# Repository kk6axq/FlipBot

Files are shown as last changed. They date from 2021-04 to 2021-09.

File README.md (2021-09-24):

# FlipBot
FlipBot is a small two wheeled robot development platform. It was developed over the Spring 2021 semester as an honors contract project for EGR102, at Arizona State University on the Polytechnic Campus, under the guidance of Dr. Daniel Frank. The goal for this project was to develop a small robot platform and to gain a better understanding of the design considerations in designing a complete system. Where possible, this project attempted to integrate components directly into the design, rather than using breakout boards or modules.
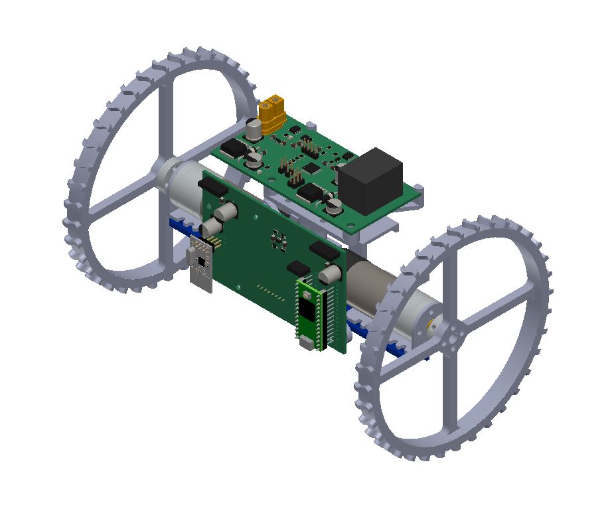
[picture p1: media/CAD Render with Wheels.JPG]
Project Photo


 ## Components
 There are several major components of FlipBot:
 * **Controller.** The robot is controlled by a wireless remote connected to a Wii Nunchuk. This provides a joystick, two buttons, and pitch/roll data that is processed by a microcontroller and sent wirelessly to the main controller onboard the robot. The controller also has onboard battery management hardware to enable operation from a single 18650 battery.
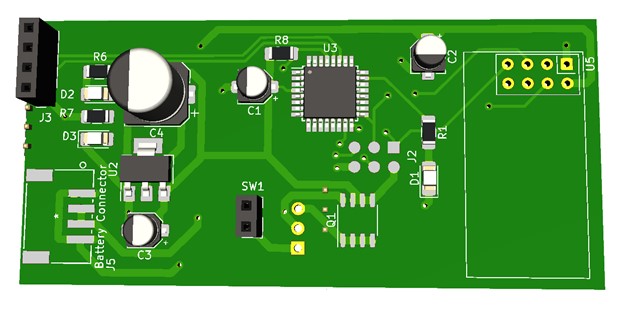
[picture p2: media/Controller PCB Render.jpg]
Controller PCB
 

 * **Wireless link.** The controller and robot use NRF24 radio modules to communicate. These operate in the 2.4GHz ISM band and provide low latency, medium range. While they have the ability to confirm packet reception, in this application the controller sends packets regardless of whether the received is in range or able to respond.
 * **Onboard Power Management.** This project was developed in conjunction with a second honors contract to develop a power management board for use with LiPo batteries. This PCB provides intelligent power monitoring capabilities on the robot. More information about this part is available in the project repository: [https://github.com/kk6axq/PowerMonitor/](https://github.com/kk6axq/PowerMonitor/).

PCB Photo

 * **Orientation Sensing.** An onboard MPU6050 accelerometer/gyro provides onboard orientation detection, enabling the controls to be reversed if the robot flips upside down.
 * **Main Board.** The main PCB interfaces to the radio, orientation sensor, and the power management board, in addition to providing motor control and processing input from the motor's encoders (not yet implemented).
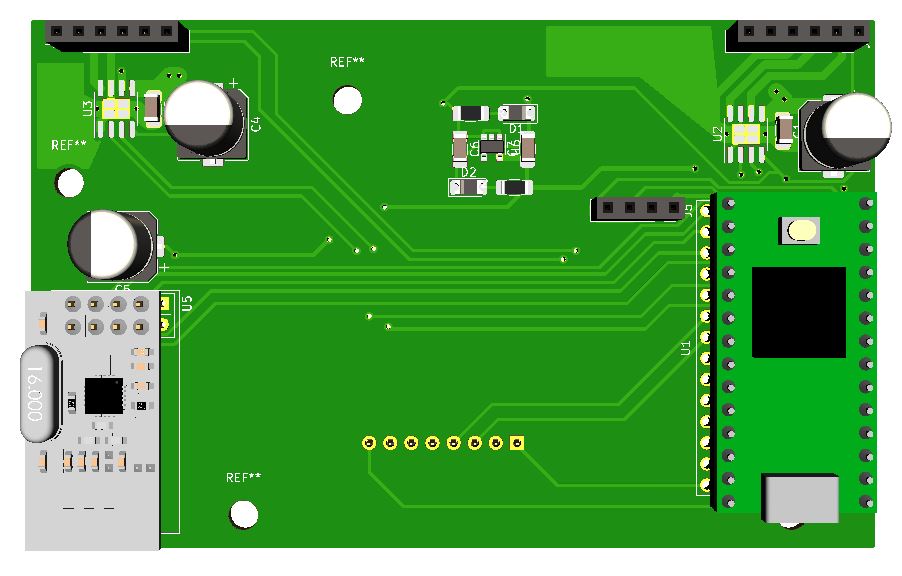
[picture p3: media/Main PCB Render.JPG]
Main PCB


## Project Status
Due to incomplete design verification and limited time, the project was not able to achieve full functionality before the end of the semester. The level converter responsible for interfacing between the motor controllers and the microcontroller was not properly matched to the application and would not properly convert, leading the motor controllers to operate sporadically.

This issue, in addition to a few minor routing decisions, is due to be fixed during a revision of the main board scheduled for Summer 2021, with the hope that the project will be functional by Fall 2021.

**Update Fall 2021:** Over the summer, the hardware design issues were mitigated within the existing PCB and a new PCB was milled for the controller. There still remain some phantom issues with controller connectivity and some larger issues with the initial current draw of the motor controllers. At this point, the project is at a holding point, and may or may not see further development.

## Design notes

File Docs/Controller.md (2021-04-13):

# Controller
The controller provides wireless teleoperation capabilities to the robot. It is powered by an ATTiny88 microcontroller with a Wii Nunchuk joystick for human input and an NRF24 radio for wireless communication.

Controller PCB Render

Controller PCB Render from KiCAD

## Input
A Wii Nunchuk controller is used for input. The controller receives 3.3V and communicates over I2C with the microcontroller. It provides a joystick, two buttons, and pitch and roll estimation, enabling multiple different control schemes. Rather than convert these into motor commands onboard, the controller sends this raw data to the robot where the selected inputs are used to calculate motor values.

## Protocol
For ease of communication, the microcontroller sends a packet consisting of a `struct` that holds all the input fields and has been converted to a byte array. The packet is sent with no acknowledgement, meaning that it will continue to send even if the robot is not in range. This could be beneficial in situations with spotty range, but comes at the cost of increased power consumption.

The `struct` and its byte array conversion are defined as follows:
```
struct RobotMsg {
  byte linear;
  byte angular;
  bool buttonC;
  bool buttonZ;
  float rollAngle;
  float pitchAngle;
};

typedef union {
  RobotMsg msg;
  byte buffer[sizeof(RobotMsg)];
} convert;
```

## Power
The controller is powered by a single 18650 Lithium Ion battery. An onboard battery manager provides a micro USB charging port and an onboard boost converter outputs a steady 5V for the main systems. The runtime on a full charge has not yet been calculated, and likely will not be, as the project used salvaged batteries that likely have lower than spec capacities.

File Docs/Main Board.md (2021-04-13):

# Main Board
The main PCB interfaces with all the major components of the robot. The core of the board is a Teensy 3.2 microcontroller, which was selected for the large number of interrupts and processing power available to handle high speed encoder measurement. The functions of the board can be roughly divided into three sections: communications, sensing, and output.

Main PCB Render

Main PCB Render from KiCAD.

## Communications
The board communicates with the controller using an NRF24 radio module. The received command packets, detailed more thoroughly in the controller documentation, are processed, fused with sensor data, and converted into motor commands.

Programming and serial monitoring is handled over the Teensy's onboard USB connector. Due to backfeeding concerns, the VUSB jumper on the Teensy was cut, meaning that it can only be programmed when the board is receiving through the external 5V supply pins.

## Sensing
The two major sensors on board are the MPU6050 accelerometer/gyro, and the power management board. The MPU6050 is currently used to measure the direction of the gravity vector for determining orientation. Depending on the orientation, the controls may be swapped to ensure the driver can continue to operate it normally.

The power management board provides connections for a monitoring port, where the Teensy could receive data on current draw, voltage, and fault states. Currently, there is no need for this in the system, and thus it is not implemented. The Teensy does not do anything that requires a shutdown procedure, so there was not a need for it to monitor the power, as it will automatically be turned off if fault conditions exist. This link could be used for possible additional features, including:
* **Safe shutdown of the payload.** If there were a payload like a Raspberry Pi, it would be useful to know when power is going to be cut so the computer could be safely shutdown.
* **Voltage indicator on controller.** Currently, the controller only communicates to the main board, but a future design could include an indicator LED for battery status and a signal could be sent to the controller to indicate that.
* **Automatic docking/recharging.** If the project were to become autonomous, monitoring the power could enable it to return to a docking station for more power.
* **Current restriction.** The main board could throttle the motors based on the current draw to optimize battery life or detect stall conditions.

## Output
The output system consists of a level converter and two motor controllers. The current revision uses the TXB0108 bidirectional level converter and two A4950 3.5A motor driver ICs. The level converter does not currently interface well with the motor controllers, likely because of the direction sensing not handling the current draw of the motor controllers well, and it will be replaced in the next revision. The motor controllers have been a bit temperamental, but appear to work well when they are installed undamaged. Together, they drive two Pololu 34:1 geared DC motors that can each provide around 63 oz-in of torque at 2.1A current draw.

Once the level shifter is replaced, the interface should be fairly straightforward, as other motor controllers using the same chipset just send normal PWM signals.

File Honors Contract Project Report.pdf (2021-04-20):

## FlipBot: Small Robot Development Platform Design Report for EGR102 Honors Enrichment Contract April 13, 2021 Lukas Severinghaus Introduction:

This project was completed for an Honors Enrichment Contract in EGR102, Foundations of Engineering Design Project II, at Arizona State University. The goal of this project was to develop a small two wheeled robot for use as a low-cost development platform in inspection applications. Rather than assembling a collection of modules, this project focused on whole system integrated development, furthering my personal interest in exploring the steps behind developing a robot system from the ground up. This honors enrichment contract was run in conjunction with a second honors enrichment contract in EGR216, under the guidance of Dr. Ayan Mallik, to develop the power management component of the robot. Ultimately, this project is still ongoing, and has been, and will be, a valuable learning experience for my personal development as an engineer. This report examines the project through the steps of the engineering design process: Empathize, Define, Ideate, Prototype, and Test.

## Empathize:

The idea from this project came from when I toured a US Army Robotics R&D lab several years ago. I saw a robot that was designed to be tossed through a window and teleoperated so that soldiers could clear a building without ever having to step foot inside. A bit more research yielded the company behind this robot, Recon Robotics, and the robot itself, the Throwbot® 2, see Figure 1 below.

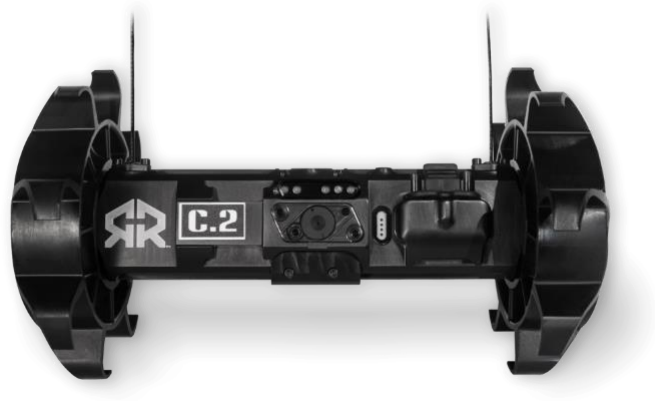
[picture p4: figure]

Figure 1. Recon Robotics Throwbot® 2 [1].

This robot retails for over $15,000, according to the GSA [2]. I was interested in learning about the development process behind a robot of this size, so I set out a few goals, and decided to build my own. In the end, I established three project criteria:

- Small size. This would allow me to use smaller components and try out surface mount components for the circuit boards.
- Drive regardless of orientation. If the robot flipped upside down, I wanted it to be able to reverse the controls so that the operator could continue to drive.
- Wireless remote control. I wanted the robot to be fully self-contained so it could run with only itself and the controller.

## Define:

Once I obtained approval for the project, the first step was to develop a block diagram. This helped define each part of the project and divided it up into small, manageable chunks. Figure 2, below, shows the block diagram for the electrical systems, where I focused most of my efforts.

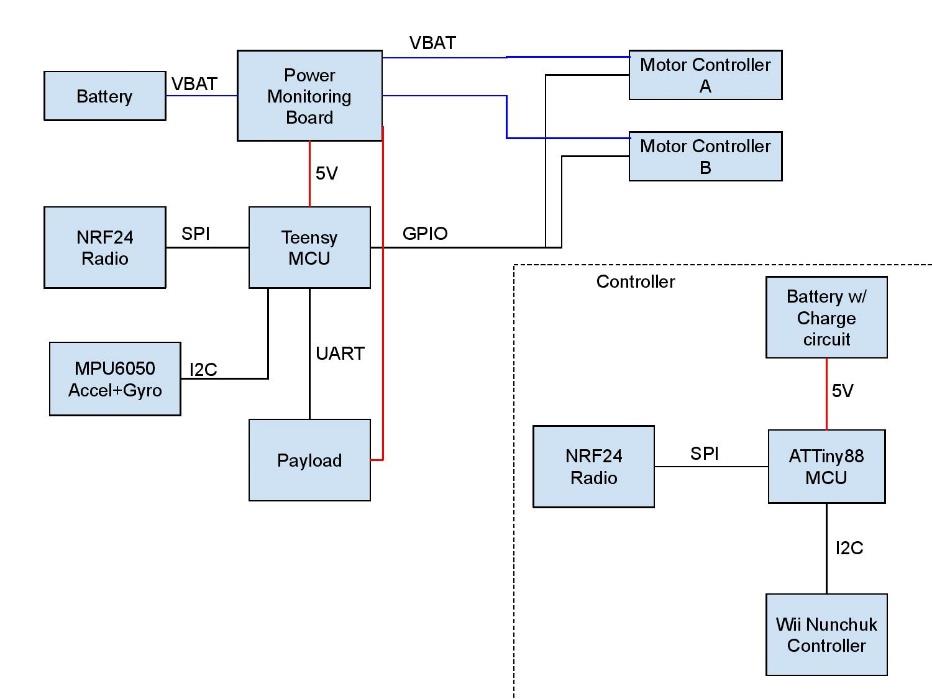
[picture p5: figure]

Figure 2. Electrical block diagram.

## Ideate:

As I finished the block diagram, I began researching each part and examining how I could implement it. I settled on a mixture of proven parts, that I had used before, and new methods, that I had not yet used. For example, I selected a Wii Nunchuk for the controller joystick, as I already had one on hand and it was more ergonomic than what I could design within the project timeframe.

For the mechanical design of the robot, I started mocking up what I wanted it to look like. The mechanical design had a large influence on the electrical design, as the printed circuit boards (PCBs) had to fit within the mechanical confines of robot. My initial CAD models were fairly crude, as I had little idea of how everything would go together, see Figure 3.

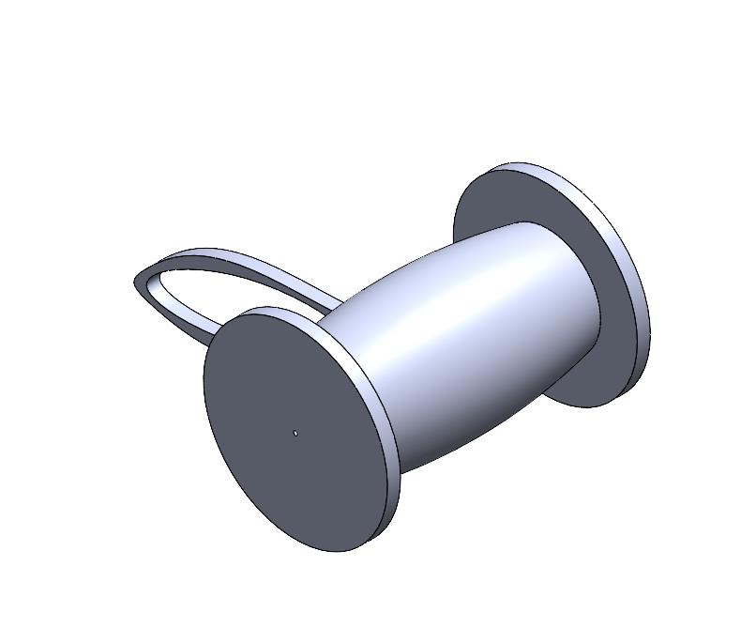
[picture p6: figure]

Figure 3. Initial CAD design with reversible tail for upside-down operation.

## Prototype:

Once I decided what parts I was going to use, I ordered a first batch of parts and assembled a breadboard prototype of the electrical system. The combined system was fairly complex and ended up covering five breadboards, but the testing helped eliminate most of the bugs in the initial designs. I used KiCAD, an open source EDA (Electronic Design Automation) program, to develop all the schematics and PCBs. These design files were then sent to the on campus PCB mill and assembled. The assembly process highlighted minor errors that had slipped past my initial breadboard testing, but ultimately no boards had to be re-milled. Figure 4 shows a render of the PCB for the wireless controller.

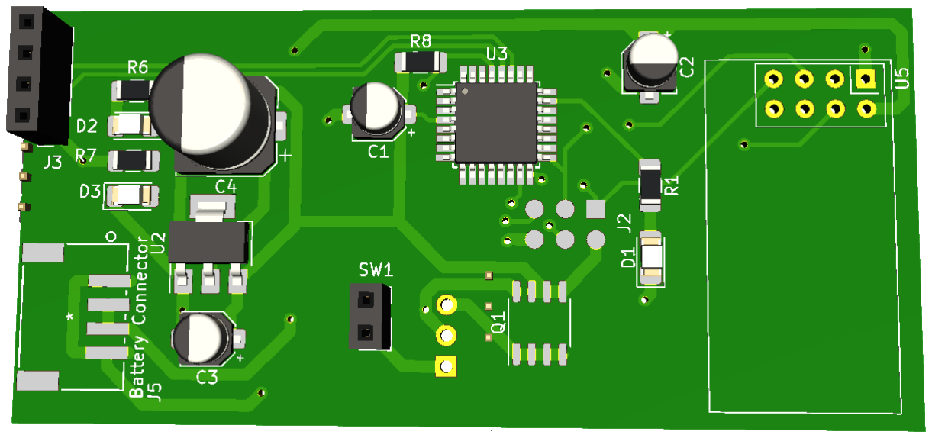
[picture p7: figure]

Figure 4. Controller PCB Render from KiCAD.

Additionally, as the PCBs reached their final forms, I used KiCAD to export STEP models of the boards into SolidWorks so I could model the mechanical design. Within the timeframe of the project, I was only able to build an initial prototype layout. While not as refined as I would have wanted, it allows easy access to all the components during testing, as shown in Figure 5.

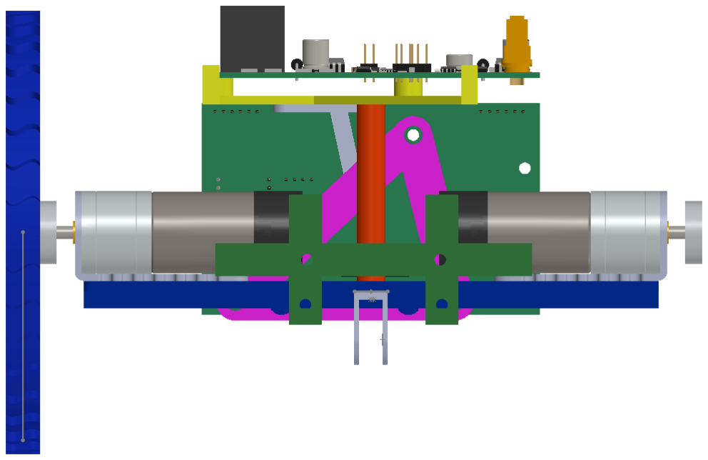
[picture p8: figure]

Figure 5. Prototype CAD assembly.

## Test:

The testing phase occupied at least half of the entire project timeline. The complexity of this project, combined with the new components I was using, made debugging a tedious, time consuming process. Ultimately, most of the bugs were ironed out, but one critical system failed to perform.

The controller’s design worked flawlessly, along with the wireless communications to the robot, and the orientation sensor, but the motor controllers, that provide power to the motors, had a fundamental design flaw. I had failed to properly breadboard test the level shifting hardware that enabled the microcontroller to communicate with the motor controllers and the parts were incompatible. By the time I came to this realization, it was too late in the semester to redesign the board, meaning the project would not be functional by the end of the semester.

## Conclusion:

Ultimately, the project was an invaluable education experience. I had the opportunity to dive into several areas I had not explored before, including:

- Multi-part 3D design and FDM printing
- Surface mount PCB design and design for integration
- Low level electrical design
- Software protocol design
- Integrated mechanical and electrical design

These are all skills that I plan to continue growing, and anticipate using, both in my education and in the workplace. Through this project, I gained an appreciation for the enormous amount of work that goes into developing a project like this. While the Honors Enrichment Contract is done, I plan to design a second revision of the electrical system to fix the issues present in the current version, with the hope that the project will be concluded in a functional state.

For more information on the project, visit: https://github.com/kk6axq/flipbot

## Acknowledgements:

The following sources were invaluable in the development of the project:

Dr. Ayan Mallik, for his assistance with the design of the power management board and for opening his lab for me to test the board.

dparson55, “dparson55/NRFLite,” GitHub. [Online]. Available: https://github.com/dparson55/NRFLite. [Accessed: 13-Apr-2021].
ElectronicCats, “ElectronicCats/mpu6050,” GitHub. [Online]. Available: https://github.com/electroniccats/mpu6050. [Accessed: 13-Apr-2021].
“Pololu - 34:1 Metal Gearmotor 25Dx67L mm MP 12V with 48 CPR Encoder,” Pololu Robotics & Electronics. [Online]. Available: https://www.pololu.com/product/4864. [Accessed: 13-Apr-2021].

## References:

[1] “THROWBOT® 2 ROBOT,” Recon Robotics. [Online]. Available: https://reconrobotics.com/products/throwbot-2-robot/. [Accessed: 13-Apr-2021].
[2] “Search Results,” U.S. General Services Administration. [Online]. Available: https://www.gsaadvantage.gov/advantage/ws/search/advantage_search?q=0:2RECONROBOTICS&db=0&searchType=0. (https://www.gsaadvantage.gov/advantage/ws/search/advantage_search?q=0:2RECONROBOTICS&db=0&searchType=0) [Accessed 13-Apr-2021].

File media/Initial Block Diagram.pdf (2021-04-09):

Battery

Power
Monitoring
Board

Motor Controller
A

Motor Controller
B

Teensy
MCU

Payload

NRF24
Radio

MPU6050
Accel+Gyro

NRF24
Radio

ATTiny88
MCU

Wii Nunchuk
Controller

Battery w/
Charge
circuit

I2C

SPI

UART

GPIO

VBAT

VBAT

SPI

I2C

5V

5V

Controller

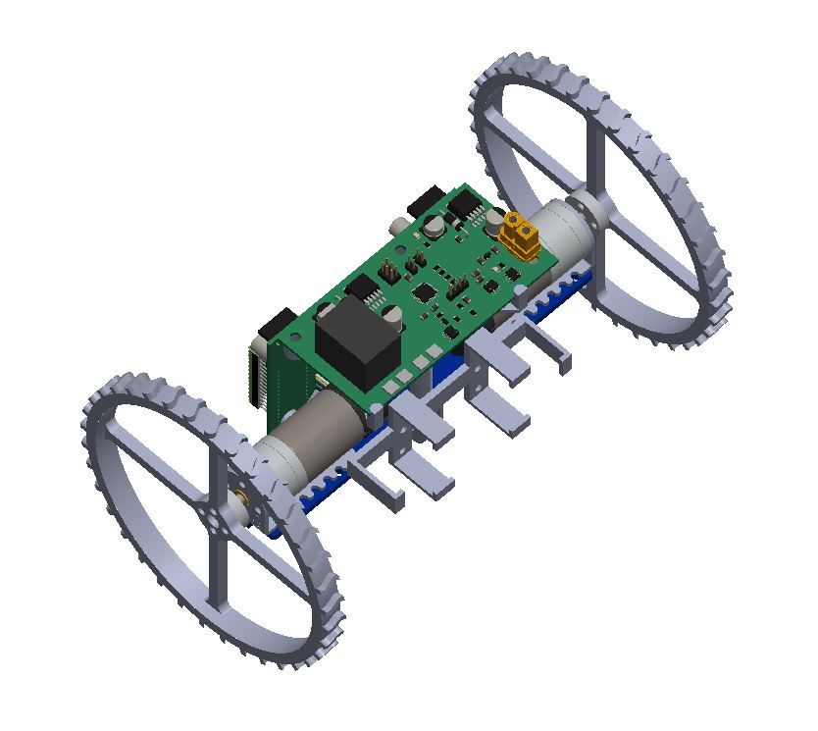
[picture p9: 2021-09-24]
media/CAD Render Rear.JPG

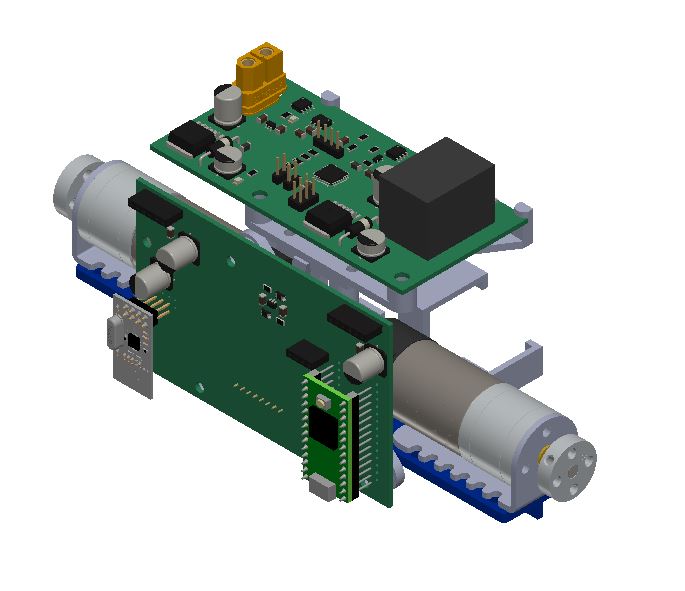
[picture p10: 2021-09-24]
media/CAD Render.JPG

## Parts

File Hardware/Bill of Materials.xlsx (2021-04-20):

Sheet: Mechanical Design
Item | Qty | Total price | Link
Gearmotor | 2 | $69.90 | https://www.pololu.com/product/4864
Hub adapter | 1 set | $6.95 | https://www.pololu.com/product/1997
Motor bracket | 2 | $14.90 | https://www.pololu.com/product/2676
Heat-set insert | ~6 | $7.49 | https://www.amazon.com/gp/product/B00Y20YLKY/
Assorted M3 hardware | Assorted | $10.99 | https://www.amazon.com/gp/product/B07CYNKLT2/

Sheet: Main Board THT
Universal Reference | Board Reference | Qty | Actual Qty | Value | Footprint | Part number | Price | Note |  | One board price |  | Line price | Status: | Ready to order
Main THT C1 C3 | C1 C3 | 2 | 10 | 0.22uF 50V X5R | THT | 445-FK28X7R1C224KN000-ND | $0.32 |  |  | $0.64 |  | $3.20
Main THT C2 C4 | C2 C4 | 2 | 10 | 100uF 50V Electrolytic | THT | 493-5916-1-ND | $0.20 |  |  | $0.41 |  | $2.05
Main THT D1 | D1 | 1 | 10 | RED |  |  |  | Already have |  | $0.00 |  | $0.00
Main THT D2 | D2 | 1 | 10 | GREEN |  |  |  | Already have |  | $0.00 |  | $0.00
Main THT J1 | J1 | 1 | 1 | Motor 1 Connector | 1x6 2.54 |  |  | Already have |  | $0.00 |  | $0.00
Main THT J2 | J2 | 1 | 1 | MPU6050 GY-521 Breakout | 1x8 2.54 |  |  | Already have |  | $0.00 |  | $0.00
Main THT J3 | J3 | 1 | 1 | Motor 2 Connector | 1x6 2.54 |  |  | Already have |  | $0.00 |  | $0.00
Main THT J4 | J4 | 1 | 1 | 5V Power | 1x2 2.54 |  |  | Amazon |  | $0.00 |  | $0.00
Main THT J5 | J5 | 1 | 1 | Payload Connector | 1x4 2.54 |  |  | Already have |  | $0.00 |  | $0.00
Main THT J6 | J6 | 1 | 1 | 12V Power | 1x2 2.54 |  |  | Amazon |  | $0.00 |  | $0.00
Main THT R1 | R1 | 1 | 10 |  |  |  |  | Already have |  | $0.00 |  | $0.00
Main THT R2 | R2 | 1 | 10 |  |  |  |  | Already have |  | $0.00 |  | $0.00
Main THT R3 R4 | R3 R4 | 2 |  | 0.1 1% 1W 2512 | THT | PPC1D.10CT-ND | $0.77 |  |  | $1.54 |  | $0.00
Main THT U1 | U1 | 1 | 1 | Teensy3.2 |  |  |  | Already have |  | $0.00 |  | $0.00
Main THT U2 U3 | U2 U3 | 2 | 2 | A4950E | SOIC-8 | 620-1400-1-ND | $2.84 | Use SMD |  | $5.68 |  | $5.68
Main THT U4 | U4 | 1 | 1 | TXB0108PWR | TSSOP20 | 296-52839-1-ND | $1.29 | Use SMD |  | $1.29 |  | $1.29
Main THT U5 | U5 | 1 | 1 | NRF24L01_Breakout | 2x4 2.54 |  |  | Amazon |  | $0.00 |  | $0.00
 |  |  |  |  |  |  |  |  | Total | $9.56 | Total price: | $12.22

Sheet: Controller THT Parts
Universal Reference | Board Reference | Qty | Actual Qty | Value | Footprint | Part number | Price | Note | One board price | Actual price | Status: | Ready to order
Controller THT C3 C1 | C3 C1 | 2 | 10 | 10uF | THT | 732-8856-1-ND | $0.10 |  | $0.20 | $1.00
Controller THT C4 | C4 | 1 | 10 | 100uF | THT | 732-8630-1-ND | $0.12 |  | $0.12 | $1.20
Controller THT C6 C5 | C6 C5 | 2 | 10 | 0.1uF | THT | 732-8962-1-ND | $0.10 |  | $0.20 | $1.00
Controller THT D1 | D1 | 1 |  | Zener 3.3V | THT | BZX85C3V3-TAPGICT-ND | $0.39 |  | $0.39 | $0.00
Controller THT D2 | D2 | 1 |  | RED |  |  |  | Already have | $0.00 | $0.00
Controller THT D3 | D3 | 1 |  | GREEN |  |  |  | Already have | $0.00 | $0.00
Controller THT J1 | J1 | 1 |  | Boost Board |  |  |  | Already have | $0.00 | $0.00
Controller THT J2 | J2 | 1 |  | AVR-ISP-6 | 2x3 2.54 |  |  | Already have | $0.00 | $0.00
Controller THT J3 | J3 | 1 |  | Nunchuk Connector |  |  |  | Already have | $0.00 | $0.00
Controller THT J4 | J4 | 1 |  | Charge Controller |  |  |  | Already have | $0.00 | $0.00
Controller THT J5 | J5 | 1 |  | Battery Connector |  |  |  | Already have | $0.00 | $0.00
Controller THT R6 | R6 | 1 |  | 330 |  |  |  | Already have | $0.00 | $0.00
Controller THT R7 | R7 | 1 |  | 220 |  |  |  | Already have | $0.00 | $0.00
Controller THT R8 | R8 | 1 |  | 10k |  |  |  | Already have | $0.00 | $0.00
Controller THT SW1 | SW1 | 1 |  | SW_SPST |  |  |  | Already have | $0.00 | $0.00
Controller THT U2 | U2 | 1 | 5 | LM1117-3.3 | THT | LM1117T-3.3/NOPB-ND | $1.64 |  | $1.64 | $8.20
Controller THT U3 | U3 | 1 | 5 | ATtiny88-AU | THT | ATTINY88-PU-ND | $1.80 |  | $1.80 | $9.00
Controller THT U4 | U4 | 1 | 2 | TXB0108DQSR | TSSOP20 | 296-52839-1-ND | $1.29 | Use SMD version | $1.29 | $2.58
Controller THT U5 | U5 | 1 |  | NRF24L01_Breakout |  |  |  | Amazon | $0.00 | $0.00
 |  |  |  |  |  |  |  |  | $5.64 | $22.98

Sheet: Controller SMD Parts
Universal Reference | Board Reference | Qty | Actual Qty | Value | Footprint | Part number | Price | Note |  | One board price | Actual price | Status: | Ready to order
Controller C3 C1 | C3 C1 | 2 | 10 | 10uF | Radial | 732-8411-2-ND | $0.17 |  |  | $0.34 | $1.70
Controller C4 | C4 | 1 | 10 | 100uF | Radial | 2616-VUJ101M1HTR-1313STR-ND | $0.12 |  |  | $0.12 | $1.20
Controller C6 C5 | C6 C5 | 2 | 10 | 0.1uF | 1206 | 732-8097-2-ND | $0.11 |  |  | $0.22 | $1.10
Controller D1 | D1 | 1 | 10 | Zener 3.3V | SMA | BZG05C3V3-M3-08GICT-ND | $0.41 |  |  | $0.41 | $4.10
Controller D2 | D2 | 1 | 10 | RED | 1206 | 160-1168-1-ND | $0.18 | Vf 2v |  | $0.18 | $1.76
Controller D3 | D3 | 1 | 10 | GREEN | 1206 | 160-1169-2-ND | $0.17 | Vf 2.1v |  | $0.17 | $1.69
Controller J1 | J1 | 1 |  | Boost Board |  |  |  | Already have |  | $0.00 | $0.00
Controller J2 | J2 | 1 | 10 | AVR-ISP-6 | 2x3 2.54 | 2057-PH2-06-UA-ND | $0.12 |  |  | $0.12 | $1.20
Controller J3 | J3 | 1 |  | Nunchuk Connector |  |  |  | Already have |  | $0.00 | $0.00
Controller J4 | J4 | 1 |  | Charge Controller |  |  |  | Already have |  | $0.00 | $0.00
Controller J5 | J5 | 1 |  | Battery Connector |  |  |  | Already have |  | $0.00 | $0.00
Controller R6 | R6 | 1 | 10 | 330 | 1206 | RMCF1206JT330RCT-ND | $0.03 |  |  | $0.03 | $0.25
Controller R7 | R7 | 1 | 10 | 220 | 1206 | RMCF1206JT220RCT-ND | $0.03 |  |  | $0.03 | $0.25
Controller R8 | R8 | 1 | 10 | 10k | 1206 | RMCF1206JT10K0CT-ND | $0.03 |  |  | $0.03 | $0.25
Controller SW1 | SW1 | 1 |  | SW_SPST |  |  |  | Already have |  | $0.00 | $0.00
Controller U2 | U2 | 1 | 5 | LM1117-3.3 | SOT223 | 488-LM1117MPX-33NOPBCT-ND | $0.45 |  |  | $0.45 | $2.25
Controller U3 | U3 | 1 | 5 | ATtiny88-AU | TQFP32 | ATTINY88-AU-ND | $1.04 |  |  | $1.04 | $5.20
Controller U4 | U4 | 1 | 5 | TXB0108DQSR | TSSOP20 | 296-52839-1-ND | $1.29 |  |  | $1.29 | $6.45
Controller U5 | U5 | 1 |  | NRF24L01_Breakout |  |  |  | Already have |  | $0.00 | $0.00
 |  |  |  |  |  |  |  |  |  | $4.41 | $27.40
C1 | Cap | 10uF |  |  | 1 | 1 | 1 |  | $0.17
C2 | Cap | 0.1uF | 1206 | 732-8097-2-ND | $0.11 | 1 | #REF! |  | #REF!
C3 | Polarized Cap | 10uF | Radial | 732-8411-2-ND | $0.17 | 1 | #REF! |  | #REF!
C4 | Polarized Cap | 100uF | Radial | 2616-VUJ101M1HTR-1313STR-ND | $0.12 | 1 | #REF! |  | #REF!
C5,C6 | Cap | 100nF | 1206 | 732-8097-2-ND | $0.11 | 1 | #REF! |  | #REF!
C7 | Polarized Cap | 47uF | Radial | 2616-VE-470M1CTR-0505STR-ND | $0.18 | 1 | #REF! |  | #REF!
D1 | Device:LED | Blue | 0603 | 732-4966-2-ND | $0.16 | 1 | #REF! |  | #REF!
D2 | Device:LED | Red | 0603 | 732-4978-2-ND | $0.14 | 1 | #REF! |  | #REF!
D3 | Device:LED | Green | 0603 | 732-4971-2-ND | $0.14 | 1 | #REF! |  | #REF!
J1 | Connector:USB_B_Micro | USB_B_Micro | Custom | WM17141CT-ND | $0.95 | 1 | #REF! |  | #REF! | See Ultralibrarian for part files
J2 | Connector:AVR-ISP-6 | AVR-ISP-6 | 0.1" pitch | 952-2121-ND | $0.26 | 1 | #REF! |  | #REF!
J3 | Connector:Conn_01x04_Female | Nunchuk Connector |  |  | $0.00 |  | #REF! |  | #REF! | Already Have
Q1 | 2n3906 | 2N3906 |  |  | $0.00 |  | #REF! |  | #REF!
R1 |  | 220k |  |  | $0.00 |  | #REF! |  | #REF!
R2 |  | 1k |  |  | $0.00 |  | #REF! |  | #REF!
R3 |  | 22 |  |  |  |  | 0 | $0.00 | $0.00
R4, R6 |  | 330 |  |  |  |  | 0 | $0.00 | $0.00
R5 |  | 33k |  |  |  |  | 0 | $0.00 | $0.00
R7 |  | 220 |  |  |  |  | 0 | $0.00 | $0.00
R8 |  | 10k |  |  |  |  | 0 | $0.00 | $0.00
SW1 |  | SW_SPST |  |  | 0 |  | 0 | $0.00 | $0.00 | Already Have
U1 | NE555 | NE555D | Package_SO:SOIC-8_3.9x4.9mm_P1.27mm |  |  |  | 0 | $0.00 | $0.00
U2 | LM1117-3.3 | LM1117-3.3 | Package_TO_SOT_THT:TO-92_Inline |  |  |  | 0 | $0.00 | $0.00
U3 | ATtiny88 | ATtiny88-AU | Package_QFP:TQFP-32_7x7mm_P0.8mm |  |  |  | 0 | $0.00 | $0.00
U4 | TXB0108 | TXB0108DQSR | Package_SON:USON-20_2x4mm_P0.4mm |  |  |  | 0 | $0.00 | $0.00
U5 | NRF24 Breakout | NRF24L01_Breakout | RF_Module:nRF24L01_Breakout |  |  |  | 0 | $0.00 | $0.00

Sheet: Main Board SMD
Universal Reference | Board Reference | Qty | Actual Qty | Value | Footprint | Part number | Price | Note | One board price |  | Line price | Status | Ready to order
Main C1 C3 | C1 C3 | 2 | 10 | 0.22uF 50V X5R | 1206 | 1276-1106-1-ND | $0.08 |  | $0.16 |  | $0.81
Main C2 C4 | C2 C4 | 2 | 10 | 100uF 50V Electrolytic |  | 493-2226-1-ND | $0.32 |  | $0.64 |  | $3.20
Main D1 | D1 | 1 | 10 | RED | 1206 | 160-1168-1-ND | $0.18 | Vf 2v | $0.18 |  | $1.76
Main D2 | D2 | 1 | 10 | GREEN | 1206 | 160-1169-2-ND | $0.17 | Vf 2.1v | $0.17 |  | $1.69
Main J1 | J1 | 1 | 1 | Motor 1 Connector | 1x6 2.54 |  |  | Already have | $0.00 |  | $0.00
Main J2 | J2 | 1 | 1 | MPU6050 GY-521 Breakout | 1x8 2.54 |  |  | Already have | $0.00 |  | $0.00
Main J3 | J3 | 1 | 1 | Motor 2 Connector | 1x6 2.54 |  |  | Already have | $0.00 |  | $0.00
Main J4 | J4 | 1 | 1 | 5V Power | 1x2 2.54 |  |  | Amazon | $0.00 |  | $0.00
Main J5 | J5 | 1 | 1 | Payload Connector | 1x4 2.54 |  |  | Already have | $0.00 |  | $0.00
Main J6 | J6 | 1 | 1 | 12V Power | 1x2 2.54 |  |  | Amazon | $0.00 |  | $0.00
Main R1 | R1 | 1 | 10 | 330 | 1206 | RMCF1206JT330RCT-ND | $0.03 |  | $0.03 |  | $0.25
Main R2 | R2 | 1 | 10 | 220 | 1206 | RMCF1206JT220RCT-ND | $0.03 |  | $0.03 |  | $0.25
Main R3 R4 | R3 R4 | 2 |  | 0.1 1% 1W 2512 | 2512 | CSRN2512FTR100CT-ND | $0.40 |  | $0.80 |  | $0.00
Main U1 | U1 | 1 | 1 | Teensy3.2 |  |  |  | Already have | $0.00 |  | $0.00
Main U2 U3 | U2 U3 | 2 | 5 | A4950E | SOIC-8 | 620-1400-1-ND | $2.84 |  | $5.68 |  | $14.20
Main U4 | U4 | 1 | 4 | TXB0108PWR | TSSOP20 | 296-52839-1-ND | $1.29 |  | $1.29 |  | $5.16
Main U5 | U5 | 1 | 1 | NRF24L01_Breakout | 2x4 2.54 |  |  | Amazon | $0.00 |  | $0.00
 |  |  |  |  |  |  |  |  | $8.97 | Total price: | $27.32

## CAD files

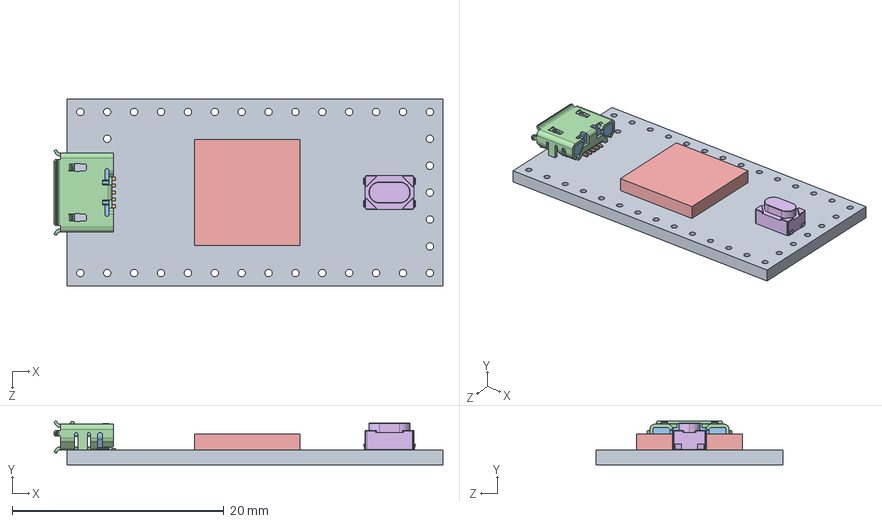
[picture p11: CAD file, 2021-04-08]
Hardware/Electrical/Custom Parts/teensy.pretty-master/Teensy_4.0_Assembly.STEP
36.8 x 4.12 x 17.7 mm
Teensy_4.0_PCB
Micro USB-B Female 5Pin SMD
NXP iMXRT1062
SKRPACE010 v4

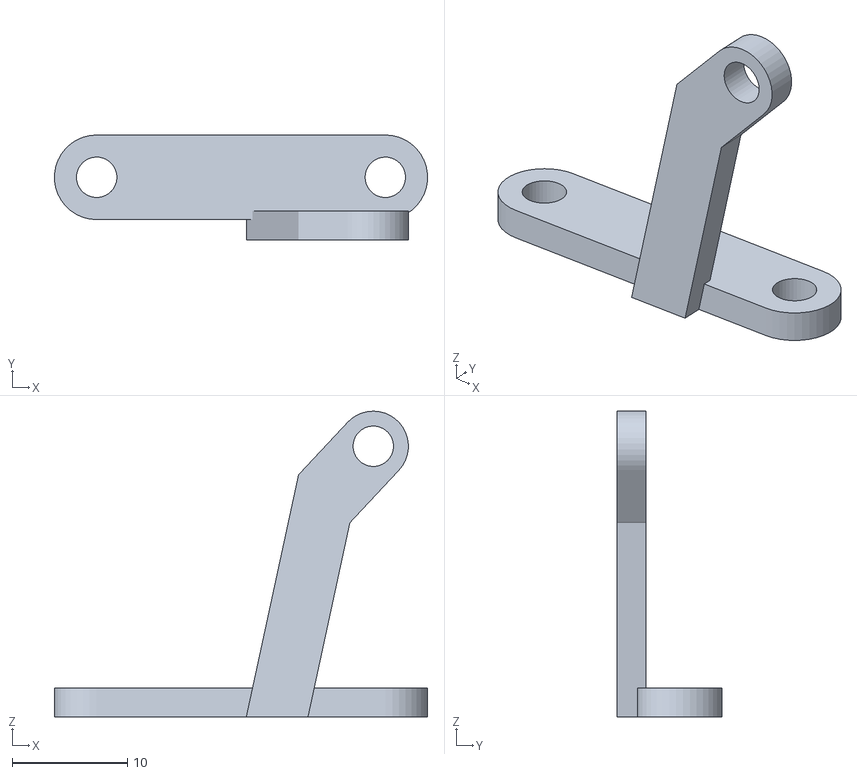
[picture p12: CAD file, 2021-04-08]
Hardware/Mechanical/Body STLs/Main to Power Bracket.STL
32.3 x 9.10 x 26.5

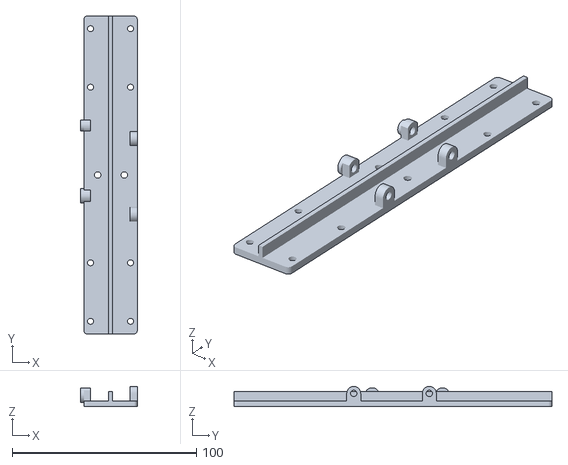
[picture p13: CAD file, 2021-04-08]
Hardware/Mechanical/Body STLs/Main Spar Bracket.STL
30.7 x 172.5 x 11.0

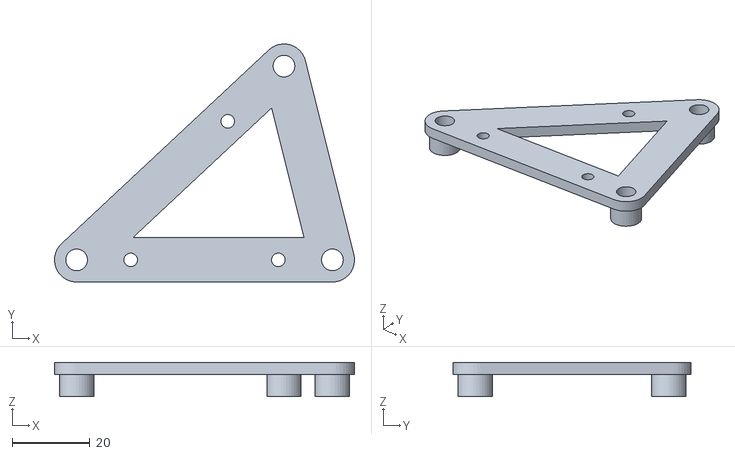
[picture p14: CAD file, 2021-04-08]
Hardware/Mechanical/Body STLs/Main Board Bracket.STL
77.4 x 61.4 x 8.89

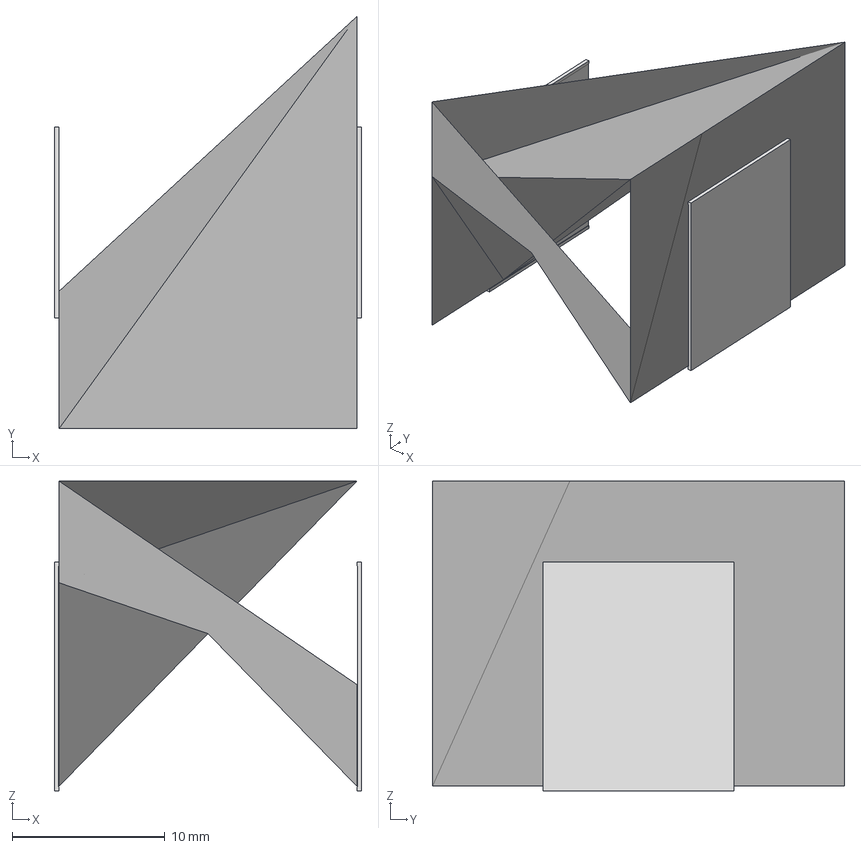
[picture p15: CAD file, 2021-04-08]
Hardware/Electrical/Custom Parts/6000B_Series_MUR.step
20.1 x 27.0 x 20.3 mm

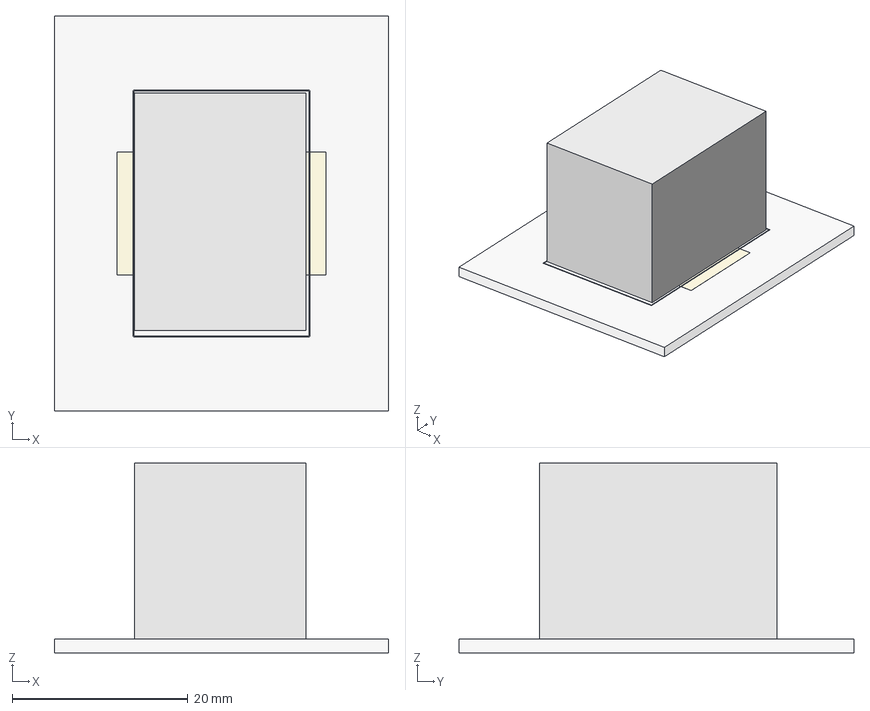
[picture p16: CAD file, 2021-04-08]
Hardware/Electrical/Custom Parts/Custom 3D Parts/Murata Inductor.FCStd
38.1 x 45.0 x 21.6 mm
FrontSilk
TopPads
Pcb

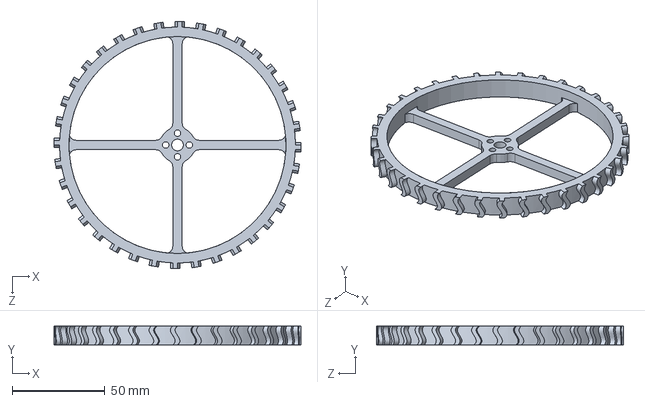
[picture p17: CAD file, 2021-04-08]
Hardware/Mechanical/New Wheel.SLDPRT
133.0 x 10.2 x 133.0 mm

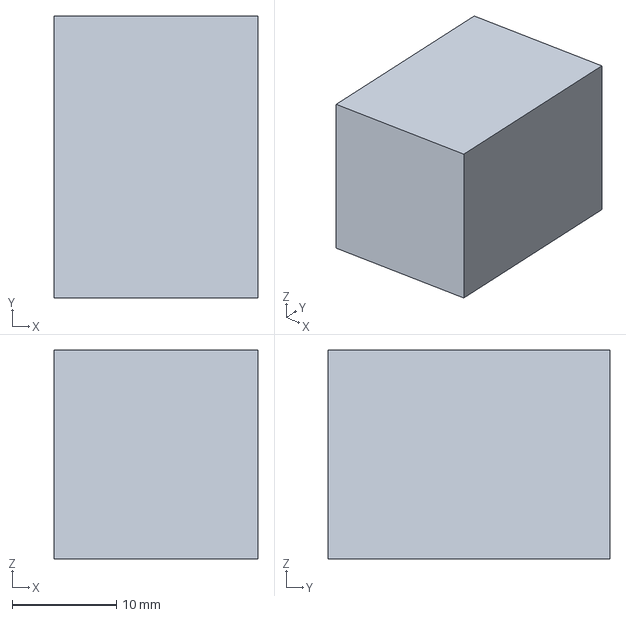
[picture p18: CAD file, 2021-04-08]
Hardware/Electrical/Custom Parts/Custom 3D Parts/Box.step
19.5 x 27.0 x 20.0 mm

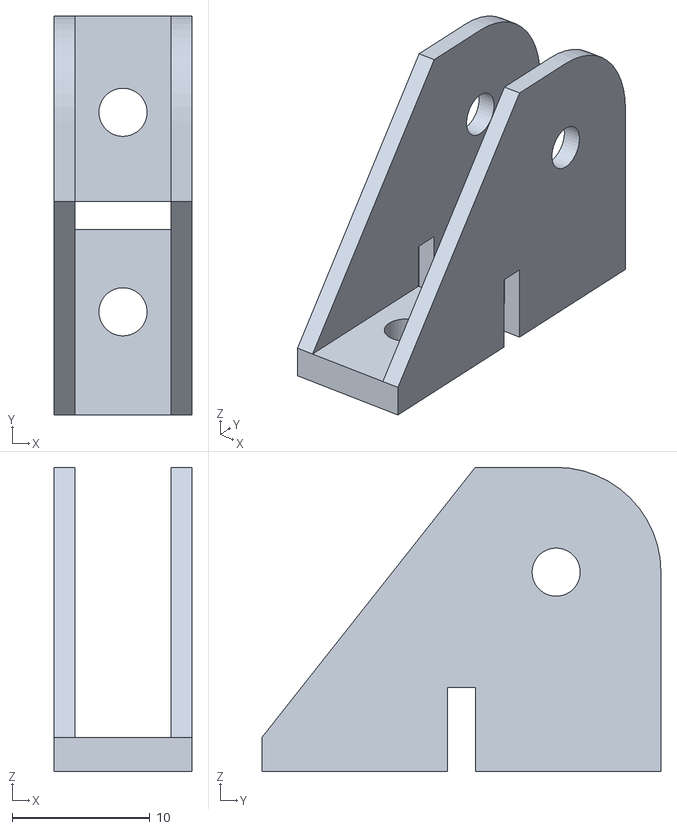
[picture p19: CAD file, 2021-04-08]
Hardware/Mechanical/Body STLs/Tail Mount.STL
10.0 x 29.0 x 22.1

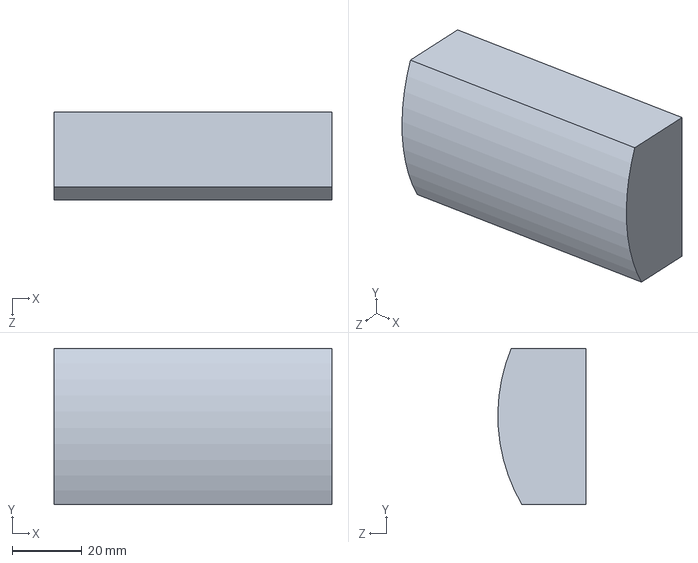
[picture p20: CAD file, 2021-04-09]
Hardware/Mechanical/Solidworks Assembly/Payload.SLDPRT
80.0 x 45.0 x 25.4 mm

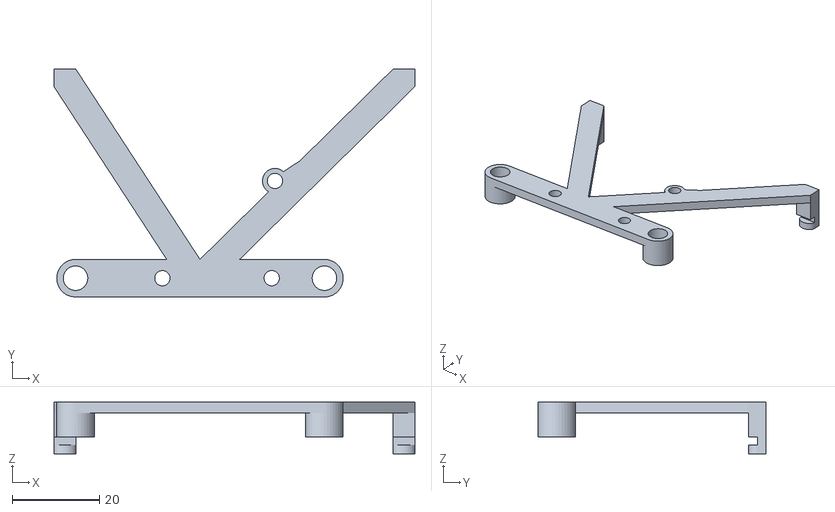
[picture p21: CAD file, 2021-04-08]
Hardware/Mechanical/Body STLs/Power Board Mount.STL
82.5 x 52.1 x 11.8

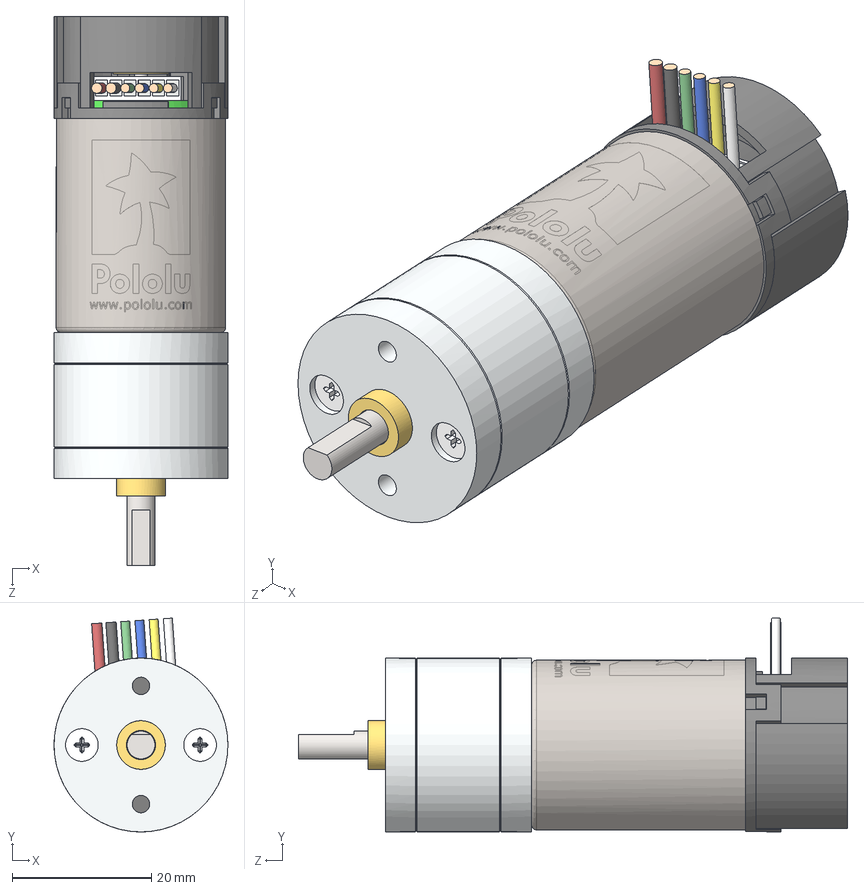
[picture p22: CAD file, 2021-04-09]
Hardware/Mechanical/Solidworks Assembly/25d-metal-gearmotor-34-47-encoder-1.step
25.0 x 30.8 x 79.0 mm

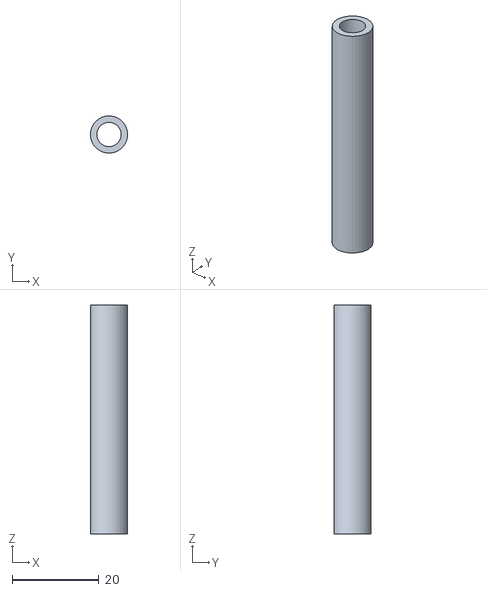
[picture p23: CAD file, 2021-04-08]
Hardware/Mechanical/Body STLs/Standoff.STL
8.60 x 8.59 x 52.9

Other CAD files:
Hardware/Mechanical/Solidworks Assembly/Main to Power Bracket.SLDPRT
Hardware/Mechanical/Solidworks Assembly/Main Spar Bracket.SLDPRT
Hardware/Mechanical/Solidworks Assembly/Main Board Bracket.SLDPRT
Hardware/Mechanical/Solidworks Assembly/Power Board Mount.SLDPRT
Hardware/Mechanical/Solidworks Assembly/Board V1.step.SLDPRT
Hardware/Mechanical/Solidworks Assembly/3in Diam Circle.SLDPRT
Hardware/Mechanical/Solidworks Assembly/Battery Holder.SLDPRT
Hardware/Mechanical/Solidworks Assembly/Battery.SLDPRT
Hardware/Mechanical/Solidworks Assembly/Standoff.SLDPRT
Hardware/Mechanical/Solidworks Assembly/Tail Mount.SLDPRT
Hardware/Mechanical/Solidworks Assembly/pololu-25d-mm-metal-gearmotor-bracket.step
Hardware/Mechanical/Solidworks Assembly/pololu-universal-aluminum-mounting-hub-for-4mm-shaft-m3-holes.step

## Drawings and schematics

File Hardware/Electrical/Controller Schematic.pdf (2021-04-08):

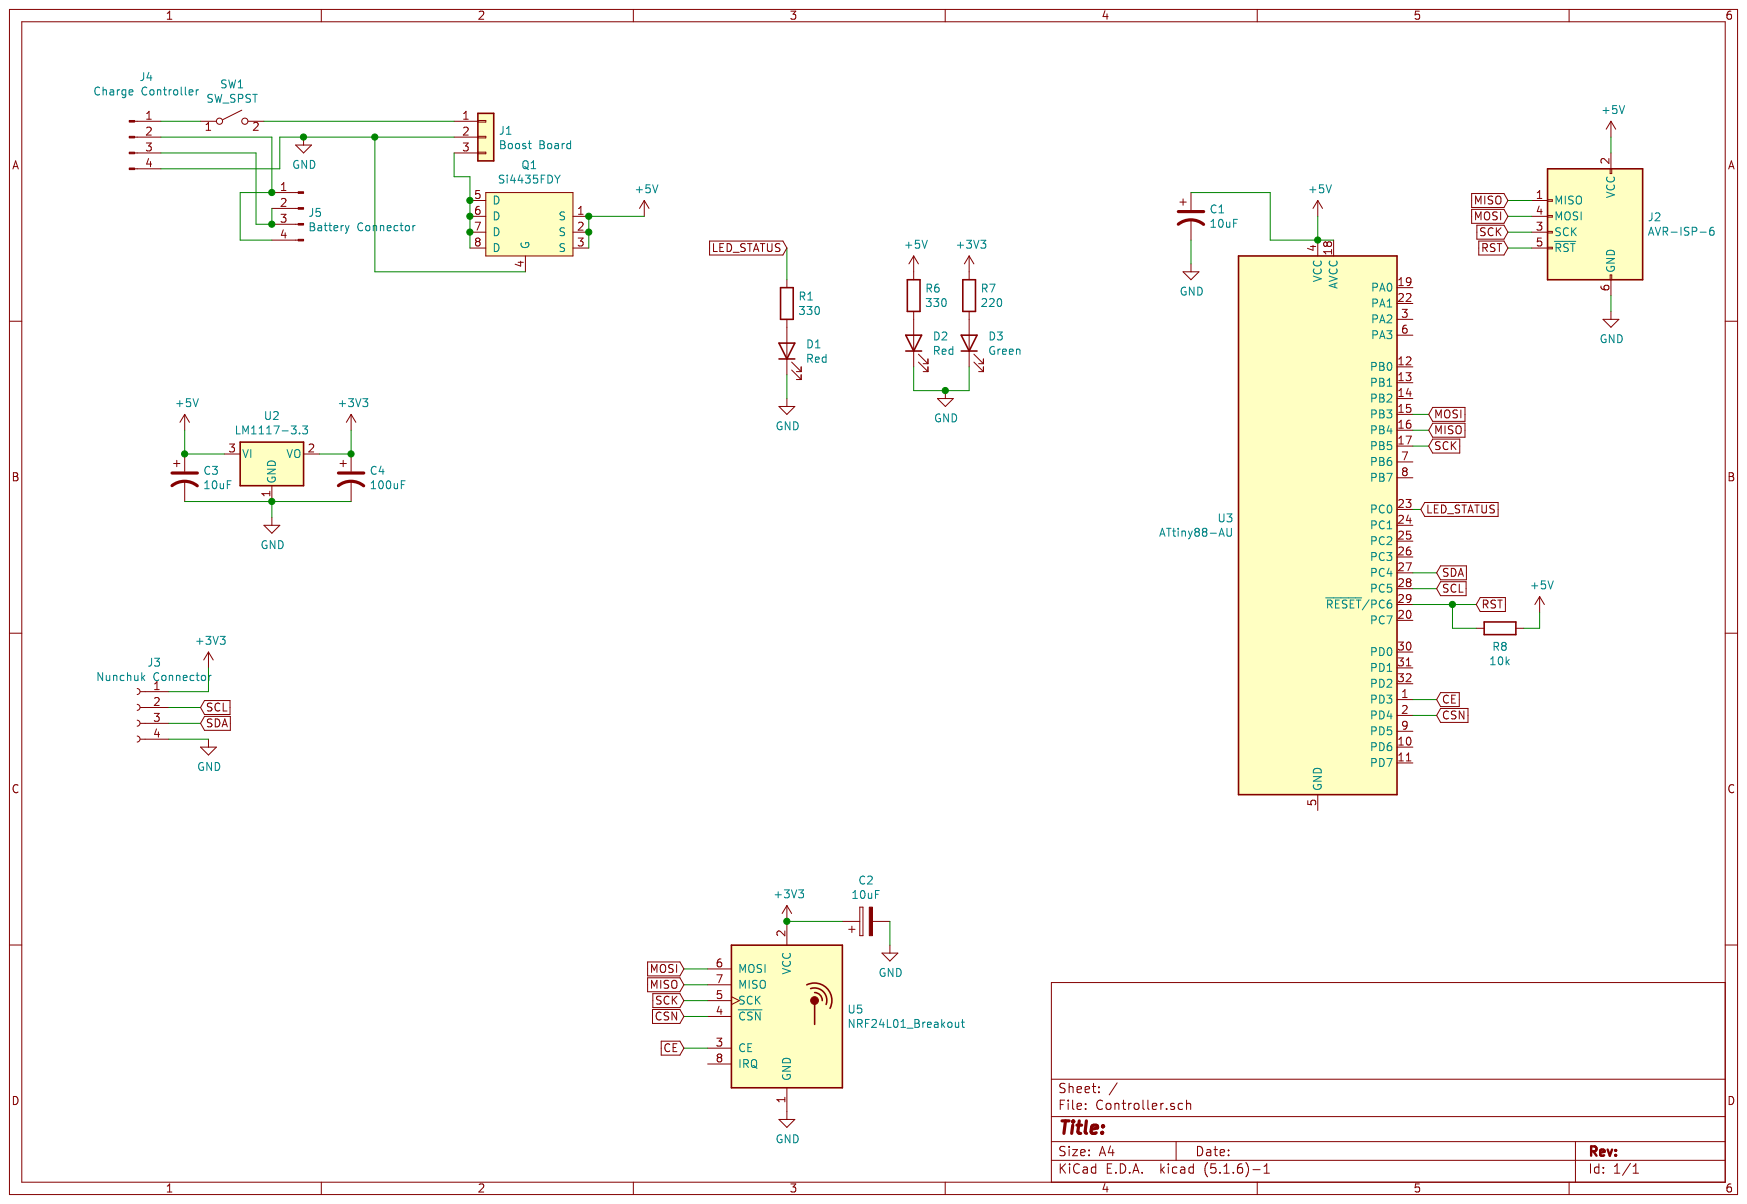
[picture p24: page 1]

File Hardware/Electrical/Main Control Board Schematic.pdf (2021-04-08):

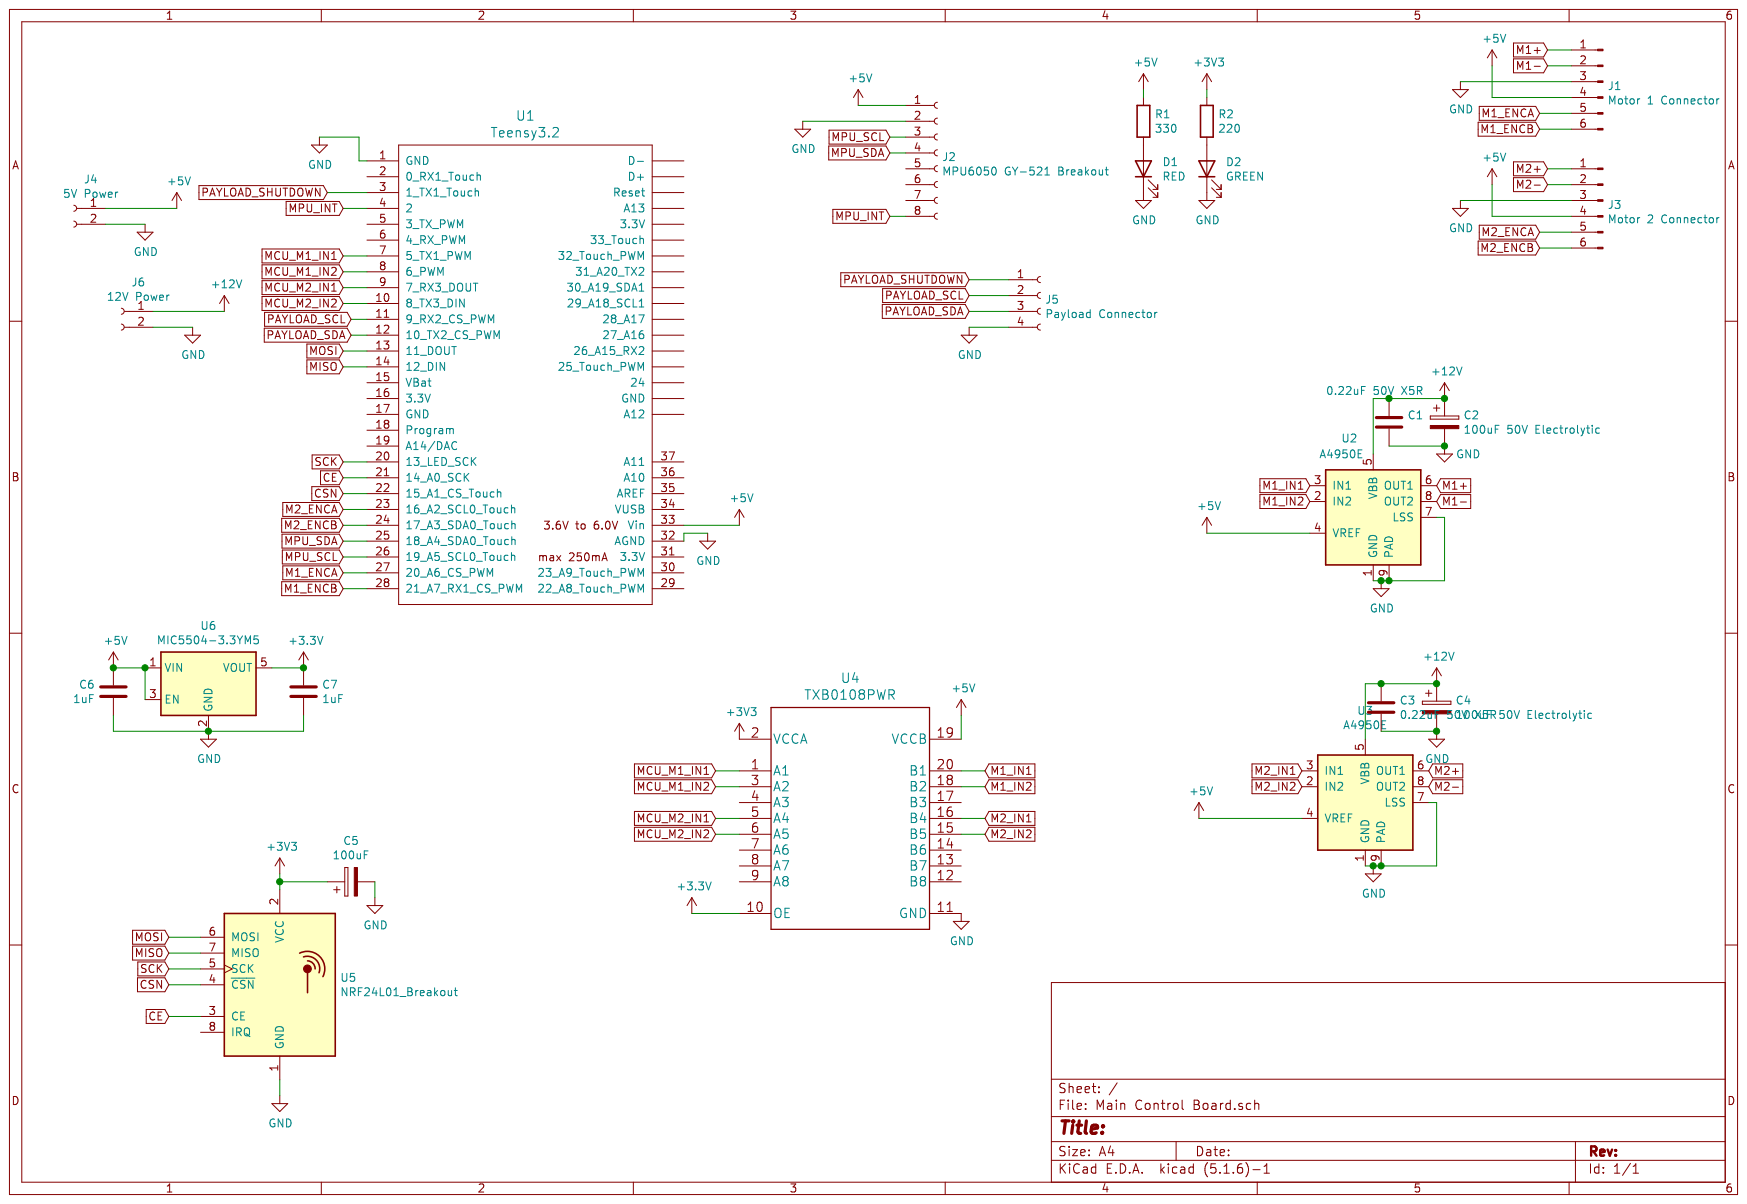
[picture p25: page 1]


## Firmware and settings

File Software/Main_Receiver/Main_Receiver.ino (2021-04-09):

/*
  Based off of Easy_RX example from NRFLite.
  NRF code based off of NRFLite library Easy_RX.ino example.
  Joystick to tank drive formula from: https://home.kendra.com/mauser/joystick.html
  MPU6050 code based off of MPU6050 library MPU6050_raw.ino example.

*/

#include <SPI.h>
#include <NRFLite.h>

#include "I2Cdev.h"
#include "MPU6050.h"
#if I2CDEV_IMPLEMENTATION == I2CDEV_ARDUINO_WIRE
#include "Wire.h"
#endif

#define Z_HIGH_THRESH 15000
#define Z_LOW_THRESH 0
MPU6050 accelgyro;
int16_t ax, ay, az;
int16_t gx, gy, gz;

const static uint8_t RADIO_ID = 0;       // Our radio's id.  The transmitter will send to this id.
const static uint8_t PIN_RADIO_CE = 14;
const static uint8_t PIN_RADIO_CSN = 15;


struct RobotMsg {
  byte linear;
  byte angular;
  bool buttonC;
  bool buttonZ;
  float rollAngle;
  float pitchAngle;
};

NRFLite _radio;
RobotMsg _radioData;
void setup()
{
  Serial.begin(115200);
  initAccelerometer();

  if (!_radio.init(RADIO_ID, PIN_RADIO_CE, PIN_RADIO_CSN))
  {
    Serial.println("Cannot communicate with radio");
    while (1); // Wait here forever.
  }
  Serial.println("Good to go");
}

void loop()
{
  if (_radio.hasData())
  {
    _radio.readData(&_radioData); // Note how '&' must be placed in front of the variable name.



    printMsg(_radioData);

    float linear = driveLinear(_radioData.linear);
    float angular = driveAngular(_radioData.angular);
    Serial.print("Linear: "); Serial.println(linear);
    Serial.print("Angular: "); Serial.println(angular);

    int left = joystickToTankDriveLeft(linear, angular);
    int right = joystickToTankDriveRight(linear, angular);

    bool flipped = readAccelerometer();
    //Assumes positive motor values are clockwise.
    if (!flipped) {
      //Normal orientation.
      //Left side reversed.
      left *= -1; //Reverse left because it needs to be ccw.
    } else {
      //Upside down orientation.
      //Motors are swapped and right side is reversed.
      int temp = left;
      left = right;
      right = -1 * temp; //Right side needs to be reversed to be ccw.
    }
    Serial.print("Flipped: ");
    Serial.print(flipped);
    Serial.print(" Motor values: Left: ");
    Serial.print(left);
    Serial.print(" Right: ");
    Serial.println(right);
  }else{
    bool flipped = readAccelerometer();
    Serial.println(flipped);
  }
}

void printMsg(RobotMsg msg) {
  String out = "Data: Linear: ";
  out += msg.linear;
  out += " Angular: ";
  out += msg.angular;
  out += " Pitch: ";
  out += msg.pitchAngle;
  out += " Roll: ";
  out += msg.rollAngle;
  out += " C: ";
  out += msg.buttonC;
  out += " Z: ";
  out += msg.buttonZ;
  Serial.println(out);
}
int driveLinear(byte input) {
  int val;
  if (input < 140 && input > 132) {
    val = 0;
  } else {
    val = map(input, 27, 230, -255, 255);
  }
  return val;
}

int driveAngular(byte input) {
  if (input < 141 && input > 129) {
    return 0;
  }
  return map(input, 27, 237, -255, 255);
}

/**
   Maps joystick x and y into tank drive
   left motor and right motor speeds.
   Assumes input is -255 to 255, outputs -255 to 255.
*/
float joystickToTankDriveRight(float x, float y) {
  x /= 2.55;
  y /= 2.55;
  x *= -1.0;
  float v = (100 - abs(x)) * (y / 100.0) + y;
  float w = (100 - abs(y)) * (x / 100.0) + x;
  float r = (v + w) / 2;
  float l = (v - w) / 2;
  return r;
}

float joystickToTankDriveLeft(float x, float y) {
  x /= 2.55;
  y /= 2.55;
  x *= -1.0;
  float v = (100 - abs(x)) * (y / 100.0) + y;
  float w = (100 - abs(y)) * (x / 100.0) + x;
  float r = (v + w) / 2;
  float l = (v - w) / 2;
  return l;
}

void initAccelerometer() {
#if I2CDEV_IMPLEMENTATION == I2CDEV_ARDUINO_WIRE
  Wire.begin();
#elif I2CDEV_IMPLEMENTATION == I2CDEV_BUILTIN_FASTWIRE
  Fastwire::setup(400, true);
#endif
  accelgyro.initialize();

}

/**
 * Checks the gravity vector from the IMU,
 * to determine the orientation. Returns
 * true if it is upside down, false otherwise.
 */
bool readAccelerometer() {

  bool up = true;
  // read raw accel/gyro measurements from device
  accelgyro.getMotion6(&ax, &ay, &az, &gx, &gy, &gz);
  Serial.print(ax);
  Serial.print(", ");
  Serial.print(ay);
  Serial.print(", ");
  Serial.println(az);
  // these methods (and a few others) are also available
  //accelgyro.getAcceleration(&ax, &ay, &az);
  //accelgyro.getRotation(&gx, &gy, &gz);
  if (az < Z_LOW_THRESH) {
    up = false;
  }
  if (az > Z_HIGH_THRESH) {
    up = true;
  }
  return !up;
  //Serial.println(up ? 1 : 0);
}

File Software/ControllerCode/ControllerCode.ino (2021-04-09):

#include <NintendoExtensionCtrl.h>
#include <SPI.h>
#include <NRFLite.h>

#define RATE 20//Hz
#define PERIOD 1000.0/RATE

#define LED_PIN 17//17
#define RADIO_CE 3//3
#define RADIO_CSN 4//4

#define RADIO_ID 1
#define DESTINATION_RADIO_ID 0

Nunchuk nc;

NRFLite _radio;
struct RobotMsg {
  byte linear;
  byte angular;
  bool buttonC;
  bool buttonZ;
  float rollAngle;
  float pitchAngle;
};

typedef union {
  RobotMsg msg;
  byte buffer[sizeof(RobotMsg)];
} convert;

long startTime = 0;

void setup() {
  //Serial.begin(9600);
  // put your setup code here, to run once:
  //Serial.println("Start");
  pinMode(17, OUTPUT);
  nc.begin();
  while(!nc.connect()){
    //Serial.println("Connecting");
    blink(100);
  }
  radioInit();
  startTime = millis();

  //while(true) digitalWrite(LED_PIN, HIGH);
}

void loop() {
  bool success = nc.update();
  if(!success){
    blink(250);
  }else{
    struct RobotMsg payload;
    payload.buttonC = nc.buttonC();
    payload.buttonZ = nc.buttonZ();
    payload.linear = nc.joyY();
    payload.angular = nc.joyX();
    payload.rollAngle = nc.rollAngle();
    payload.pitchAngle = nc.pitchAngle();
    //Serial.print("Linear: ");
    //Serial.print(payload.linear);
    //Serial.print(" Angular: ");
    //Serial.println(payload.angular);
    convert converter;
    converter.msg = payload;
    //Serial.print("\t\tPayload: ");
    for(int i = 0; i < sizeof(payload); i++){
      //Serial.print( int(converter.buffer[i]) ); Serial.print(", ");
      
    }
    //Serial.println();
    sendMsg(payload, sizeof(payload));
  }
  int loopTime = millis() - startTime;
  if(loopTime < PERIOD){
    //Serial.print("Delaying for: ");
    //Serial.println(PERIOD - loopTime);
    delay(PERIOD - loopTime);
  }
  startTime = millis();
}

void blink(int time){
  digitalWrite(LED_PIN, HIGH);
  delay(time);
  digitalWrite(LED_PIN, LOW);
  delay(time);
}



void sendMsg(RobotMsg data, int length){
  bool result = _radio.send(DESTINATION_RADIO_ID, &data, length, NRFLite::NO_ACK);
  if(!result){
    blink(1000);
//    Serial.println("Error sending");
  }else{
    blink(5);
  }
}



void radioInit(){
  if(!_radio.init(RADIO_ID, RADIO_CE, RADIO_CSN)){
  //  Serial.println("Error communicating with radio");
    while(1) blink(500);
  }
}

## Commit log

2021-04-08 Add Hardware Files
    [6000B_Series_MUR.step, Box.step, Controller.kicad_pcb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]
2021-04-09 Add more hardware and software files
    [25d-metal-gearmotor-34-47-encoder-1.step, 3in Diam Circle.SLDPRT, 6000B_Series_MUR.step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]
2021-04-20 Add BOM
    [Bill of Materials.xlsx]
